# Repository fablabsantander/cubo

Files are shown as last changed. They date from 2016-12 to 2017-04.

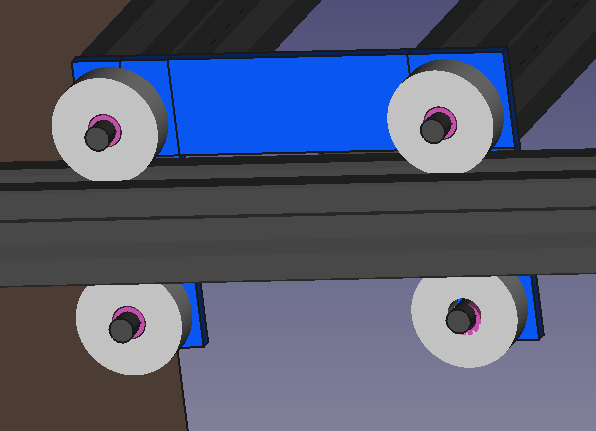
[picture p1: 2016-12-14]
IMG/image-1.png

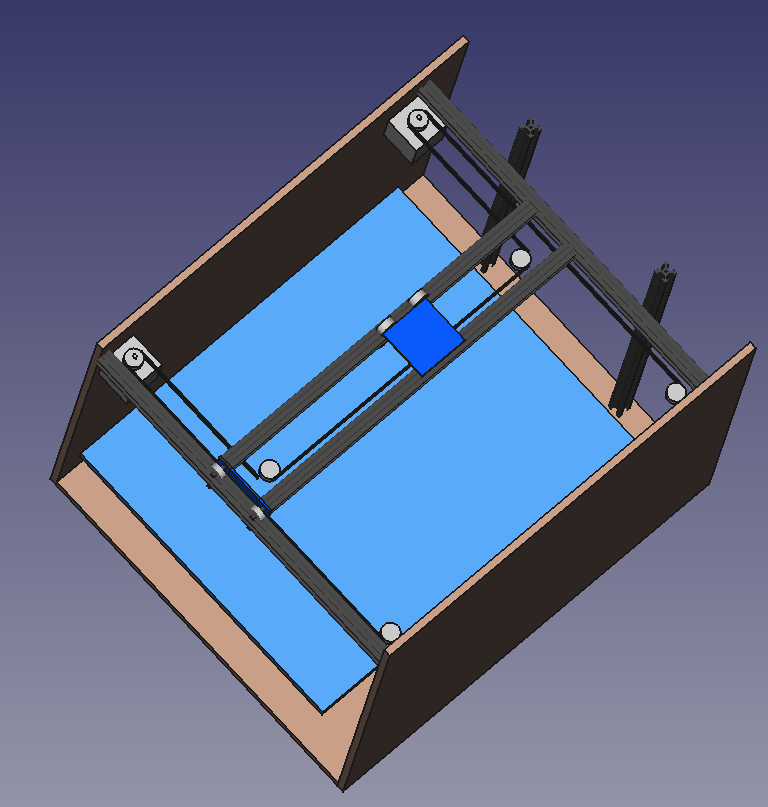
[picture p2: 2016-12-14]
IMG/image.png

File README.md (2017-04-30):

# cubo
cubo design
real build

Machine for 3D printing (and laser engraving).

Some members of the FabLab Santander have committed themselves to build the machines of the lab in a co-creation process.
This machine is a cubic shape 3D printer with option of laser engraving.
This side size of the cube is more or less 500mm.
The purpose of the design is to get a big size open source 3D printer, nice-looking, easy to build, robust with metal profiles and standart bearings (not the linear ones...).
The main design software is openscad which allow a natural integration in CVS or github software repositories.
The design is parametrized as much as possible. The elements choosen for the first version are:

- RatRig profiles
- 627 bearings
- wood/plexiglass plates
- complex pieces are 3D printed
- the XY movement follow the "coreXY" scheme (see www.corexy.com)

Coding conventions for openscad files:
- try to comment every decision in the design
- try to use parameters for all dimensions such we have not to redesign when changing one piece dimension.
- minimize the number of parameters
- put the parameters at the beginning of the file with explicit names and comments
- then put the modules to be 3D printed (commented)
- then put the module called "ensemble" that gather all the pieces
- then put eventually cut views
- then put the modules

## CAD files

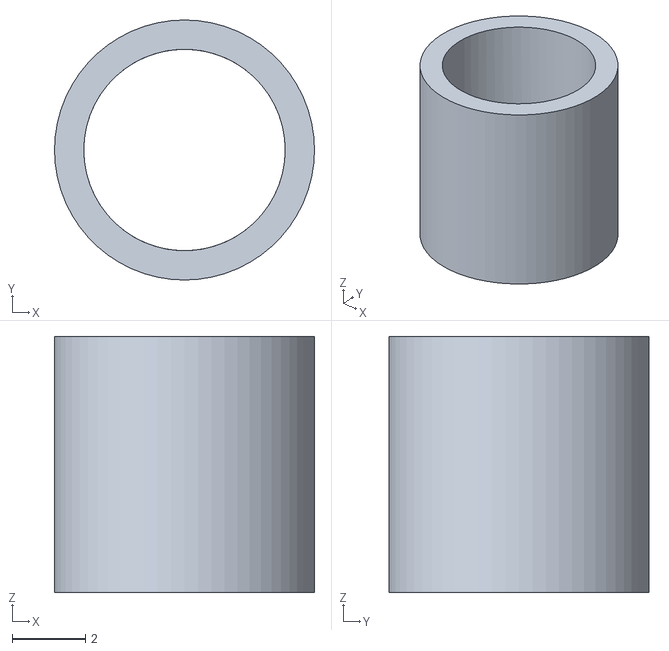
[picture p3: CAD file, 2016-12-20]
anillo_rodamiento_627.obj
7.10 x 7.10 x 7.00

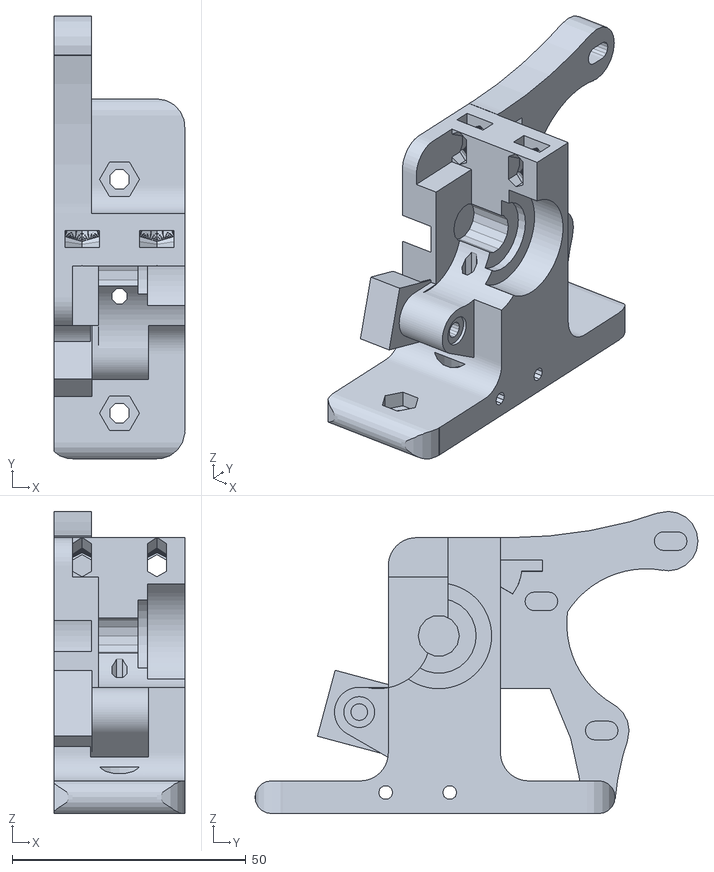
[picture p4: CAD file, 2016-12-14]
extruder.stl
28.0 x 94.7 x 64.6

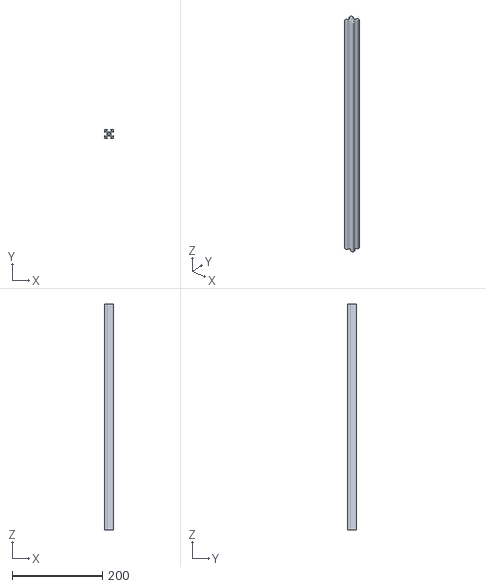
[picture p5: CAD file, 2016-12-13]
profil_ratrig_500mm.stl
20.0 x 20.0 x 500.0

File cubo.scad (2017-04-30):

//FabLab Santander
//machine "cubo"
//licence creative common 

//profile:
profilex_length=500;
profiley_length=500;
profilez_length=500;
profile_size=20;
profile_screw_D=5;

// height
h=560;//side plate height

//plates :
th=10; //side and base plate thickness
back_th=3;//back plate thickness


//bearing 627:
bearing_D=22;
bearing_dint=7;
bearing_th=7;



//distance between the 2 guides x
inter_guides_x=profiley_length/2+10+bearing_th/2;
echo("distance between the 2 guides x:",2*inter_guides_x,"mm");
//x trail:
dx_guidey=60;//distance between the 2 guides y
dz_guidey=profile_size/2+bearing_D/2-1.5;//profile_size-0.5;
//x trail plate:
xtrailPlateThickness=3;
//head:
headPlateThickness=5;
headPlate_dx=dx_guidey-profile_size-2;
headPlate_dy=80;

//stepper motor nema17:
motNema17Side=42;
motNema17Dep=47.65;
motNema17AxisD=5;
motNema17AxisL=26;
motNema17ScrewFixD=3;
motNema17ScrewsDist=31;
motNema17FrontD=22;
motNema17FrontH=1.5;
//motor pulley GT2
pulleyTeethDiameter=12;
pulleyDiameter=16;
pulleyThickness=16;
//belts:
belt_th=6;//belt thickness
belt_thi=2;//belt thickness
z_belts=3;
//half distance between pulley in y direction
inter_pulleys_y=profiley_length*0.46;
//head plateform parameters:
head_bearing_axis_z=profile_size/2+bearing_D/2-1.5;

//PLA coil:
d_PLA_coil_inner=51;
d_PLA_coil_outer=200;
h_PLA_coil=72;


head_X=150;
head_Y=0;



//the CUBE machine mounted:
//ensemble();
//structure();


//------------  3D print: -------------------
//rotate([-90,0,0])xtrailPlate();
//bearingPusher();
//bearingAdaptor(); 
//stepper_holder();
//pulley_holder();
//rotate([180,0,0])head_plateform();
//rotate([-90,0,0])head_bearing_holder();
//pulley_washer();
//rotate([90,0,0])PLA_pulley_holder();
//rotate([0,90,0])PLA_pulley();
PLA_coil_holder();
//------------  3D print: -------------------

//dim cube:
cube_length_x = profilex_length+2*thickness_panel;
cube_length_y = profiley_length+2*profile_size;
h_stop_extruder = 120;
height_cube = profilex_length+h_stop_extruder+2*thickness_panel;

//z system:
inter_zguides=300;




module plates()
{
//translate([profilex_length/2,0,0]) provisory_side_plate();
//mirror([1,0,0])translate([profilex_length/2,0,0]) provisory_side_plate();
//translate([profilex_length/2,0,0]) side_plate();
//for (c=[0,1]) mirror([c,0,0])translate([profilex_length/2,0,0]) side_plate();

//side metalic bar for the XY system		
bar_th=4; 

//front plate:
dx=profilex_length+2*bar_th;
l3=130;//front plate height

dx_base=profilex_length+2*th+2*bar_th;
dy=profiley_length+50;
//l1=100; //side plates width
h2=200;//side plate noze height
backSpace=50;//space at the back for the Z system
dy2=profiley_length+50;//side plate depth
dy_nose=dy2*0.25;//nose depth
rad=dy_nose/2;
hup=profile_size*2.5;
	
//side metalic bar for the XY system 
color([0.8,0.8,0.8])for (c=[0,1]) mirror([c,0,0])
{
	difference()
	{
	translate([profilex_length/2,-dy2/2,-profile_size/2])cube([bar_th,dy2,profile_size]);
	for (y=[-1,1])translate ([profilex_length*0.3,y*(inter_guides_x),0])rotate([0,90,0])cylinder(h=200,r=5/2,$fn=20);	}
}
color=[.6,.6,.9];
//base plate:
color(color+[0.1,0,0]) translate([-dx_base/2,-dy2/2+dy_nose,-h])cube([dx_base,dy2-dy_nose+backSpace,th]);
//front plate;
//color(color-[0.1,0,0])translate ([-dx/2,-dy2/2+dy_nose,-h+th])rotate([16,0,0]) cube([dx,th,l3]);

//back plate;
color(color-[0.1,0,0])translate ([-dx/2-th,-dy2/2+dy_nose+dy2-dy_nose+backSpace,-h])cube([dx+2*th,back_th,hup+h]);

//side plates
color(color)for (c=[0,1]) mirror([c,0,0])translate([profilex_length/2+th+bar_th,0,0]) 
{
rotate([0,-90,0])linear_extrude(height=th)
	{
	polygon([
		// z  y
		[-profile_size*4,-dy2/2],
		[hup,-dy2/2],
		[hup,dy2/2+backSpace],
		[-h+th,dy2/2+backSpace],
		[-h+th,-dy2/2+dy_nose]
		]);
	}
}
//side plates
//for (c=[0,1]) mirror([c,0,0])translate([profilex_length/2,0,0]) 
//	{
//	color("orange")
//	difference()
//		{
//		union()
//			{
//			//top:
//			translate ([0,-dy2/2,-h2+20]) cube([thickness_panel,dy2,h2]);
//			//bottom:	
//			translate ([0,-dy2/2+dy_nose,-h+20]) cube([thickness_panel,dy2-dy_nose,h]);
//			//round
//			translate ([0,-dy2/2+rad,-h*0+20-h2])rotate([0,90,0])cylinder(r=rad,h=th,$fn=30);
//			}
//		for (y=[-1,1])translate ([profilex_length*0.3,y*(inter_guides_x),0])rotate([0,90,0])cylinder(h=200,r=5/2,$fn=20);
//		}
//	}



echo("base plate size (mm):",dx_base,dy2-dy_nose+backSpace,th);
echo("side plates (2x) size (mm):",dy2/2+backSpace-(-dy2/2),hup-(-h+th),th);
echo("dy nose (mm):",dy_nose);
//echo("back plate size (mm):",dx-2*th,l2,th);
echo("front plate size (mm):",dx,l3,th);

	
}




module ensemble()
{
//the clothes of the machine:
//cover();
    
plates();

provisory_zsystem();
 
	
//guides for x translation
for (i=[-1,1])
translate([-profilex_length/2,i*(-profiley_length/2-10-bearing_th/2),0])rotate([0,90,0])color([0.2,0.2,0.2])import ("profil_ratrig_500mm.stl");

//guides for y translation
translate([head_X,0,0])//Y carriage ensemble
{
for (i=[-1,1])
    {
    //guides y
    translate([i*-dx_guidey/2,profiley_length/2,dz_guidey])rotate([90,0,0])color([0.2,0.2,0.2])import ("profil_ratrig_500mm.stl");
    //bearings:
    for (j=[-1,1]) translate([i*-dx_guidey/2,j*(profiley_length/2+bearing_th/2+10),dz_guidey])rotate([90,0,0])
        {
        bearing();
        bearingAdaptor();    
        }
    //screw for bearings:
     color([0.4,0.4,0.4])for (j=[-1,1])translate([i*-dx_guidey/2,j*(profiley_length/2+10),dz_guidey])rotate([90,0,0])cylinder(r=profile_screw_D/2,h=20,$fn=30,center=true);
    }
	 
//lower bearings 
for (j=[-1,1]) translate([0,j*(profiley_length/2+bearing_th/2+10),-dz_guidey])
	{
	rotate([90,0,0])bearing();
	rotate([90,0,0])bearingAdaptor();    
	//screw for bearings:
	color([0.4,0.4,0.4])translate([0,-profile_size/2,0])rotate([90,0,0])cylinder(r=profile_screw_D/2,h=30,$fn=30,center=true);
   }
	 
	 
	 
//xtrail side plates:
translate([0,profiley_length/2+xtrailPlateThickness/2,dz_guidey+profile_size/2])
	{
	xtrailPlate();
	bearingPusher();
	}
mirror([0,1,0]) translate([0,profiley_length/2+xtrailPlateThickness/2,dz_guidey+profile_size/2])
	{
	xtrailPlate();
	bearingPusher();
	}
  
//head:
translate([0,head_Y,dz_guidey])
	{
	//bearings
	 for (x=[-1,1]) for (y=[-1,1]) translate([x*dx_guidey/2,y*headPlate_dy*0.4,head_bearing_axis_z])rotate([0,0,90]) rotate([90,0,0])bearing();
	 for (x=[-1,1])  translate([x*dx_guidey/2,0,-head_bearing_axis_z])rotate([0,0,90]) rotate([90,0,0])bearing();
	//head plateform:
	head_plateform();
	//head bearings holder (with springs to push down the bearings
	for (y=[-1,1])translate([0,y*headPlate_dy*0.44,head_bearing_axis_z])head_bearing_holder();
	 // extuder:    
	//prusa i2 extruder:
	//translate([0,0,headPlateThickness])color("blue")rotate([0,0,0])import("extruder.stl");  
	//extruder head alone:
	color("gray")translate([0,0,5])extruder();  
	}

//pulleys fixed on the Y guides:
for (x=[-1,1])for (y=[-1,1])translate([-x*dx_guidey/2,y*(profiley_length*0.45-bearing_D),z_belts]) 
		{
		bearing();
		translate([0,0,-bearing_th])pulley_washer();
		}
}//end of X carriage ensemble

translate([0,0,z_belts])
{

for (c=[0,1]) mirror([0,c,0])
	{
	//stepper holder:
	translate([-profilex_length/2+motNema17Side/2,inter_pulleys_y,-17])stepper_holder();
	//pulley holder:
	translate([profilex_length*0.47,-inter_guides_x-profile_size/2,-17])pulley_holder();
	}

for (y=[-1,1])
	{
	//stepper motors:
	translate([-profilex_length/2+motNema17Side/2,y*inter_pulleys_y,-17])rotate([0,-90,0])color("skyblue")motor_nema17();
	//GT2 pulleys on steppers:
	color("grey")translate([-profilex_length/2+motNema17Side/2,y*inter_pulleys_y,-pulleyThickness*0.7]) pulley();//bearing();
	//pulleys on the other side:
	translate([profilex_length*0.47,y*inter_pulleys_y,0]) bearing();
	}
	
	//pulleys on the other side:
	for (c=[0,1]) mirror([0,c,0])translate([profilex_length*0.42,inter_pulleys_y-20,0]) bearing();
	
	


//belt at right
color("blue")for (c=[0,1]) mirror([0,c,0])translate([profilex_length*0.47+bearing_D/2,inter_pulleys_y*0.05,-belt_th/2])rotate([2,0,0])cube([belt_thi,inter_pulleys_y*1.9,belt_th],center=true);
//belts:
for (y=[-1,1])
	{
	color("blue")translate([-profilex_length/2+motNema17Side/2,y*(inter_pulleys_y+bearing_D/2),-belt_th/2])cube([inter_pulleys_y*2,belt_thi,belt_th]);
	color("blue")translate([-profilex_length/2+motNema17Side/2,y*(inter_pulleys_y-bearing_D/2),-belt_th/2])cube([profiley_length/2,belt_thi,belt_th]);
	color("blue")translate([head_X+dx_guidey/2,y*(inter_pulleys_y-bearing_D/2),-belt_th/2])cube([profiley_length/2-head_X-dx_guidey,belt_thi,belt_th]);
	}
//belts on the x rail:
color("blue")for (x=[-1,1]) translate([head_X-x*dx_guidey/2+x*bearing_D/2,-inter_pulleys_y+bearing_D,-belt_th/2])cube([belt_thi,inter_pulleys_y*2-bearing_D*2,belt_th]);

}

translate([-profilex_length/2+40,-100,-h+th])rotate([0,0,90])
{
PLA_pulley_holder();
PLA_pulley();
}

translate([0,0,-h+th])rotate([0,0,90])
{
color("black")translate([0,0,5])PLA_coil();
PLA_coil_holder();
}



}
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

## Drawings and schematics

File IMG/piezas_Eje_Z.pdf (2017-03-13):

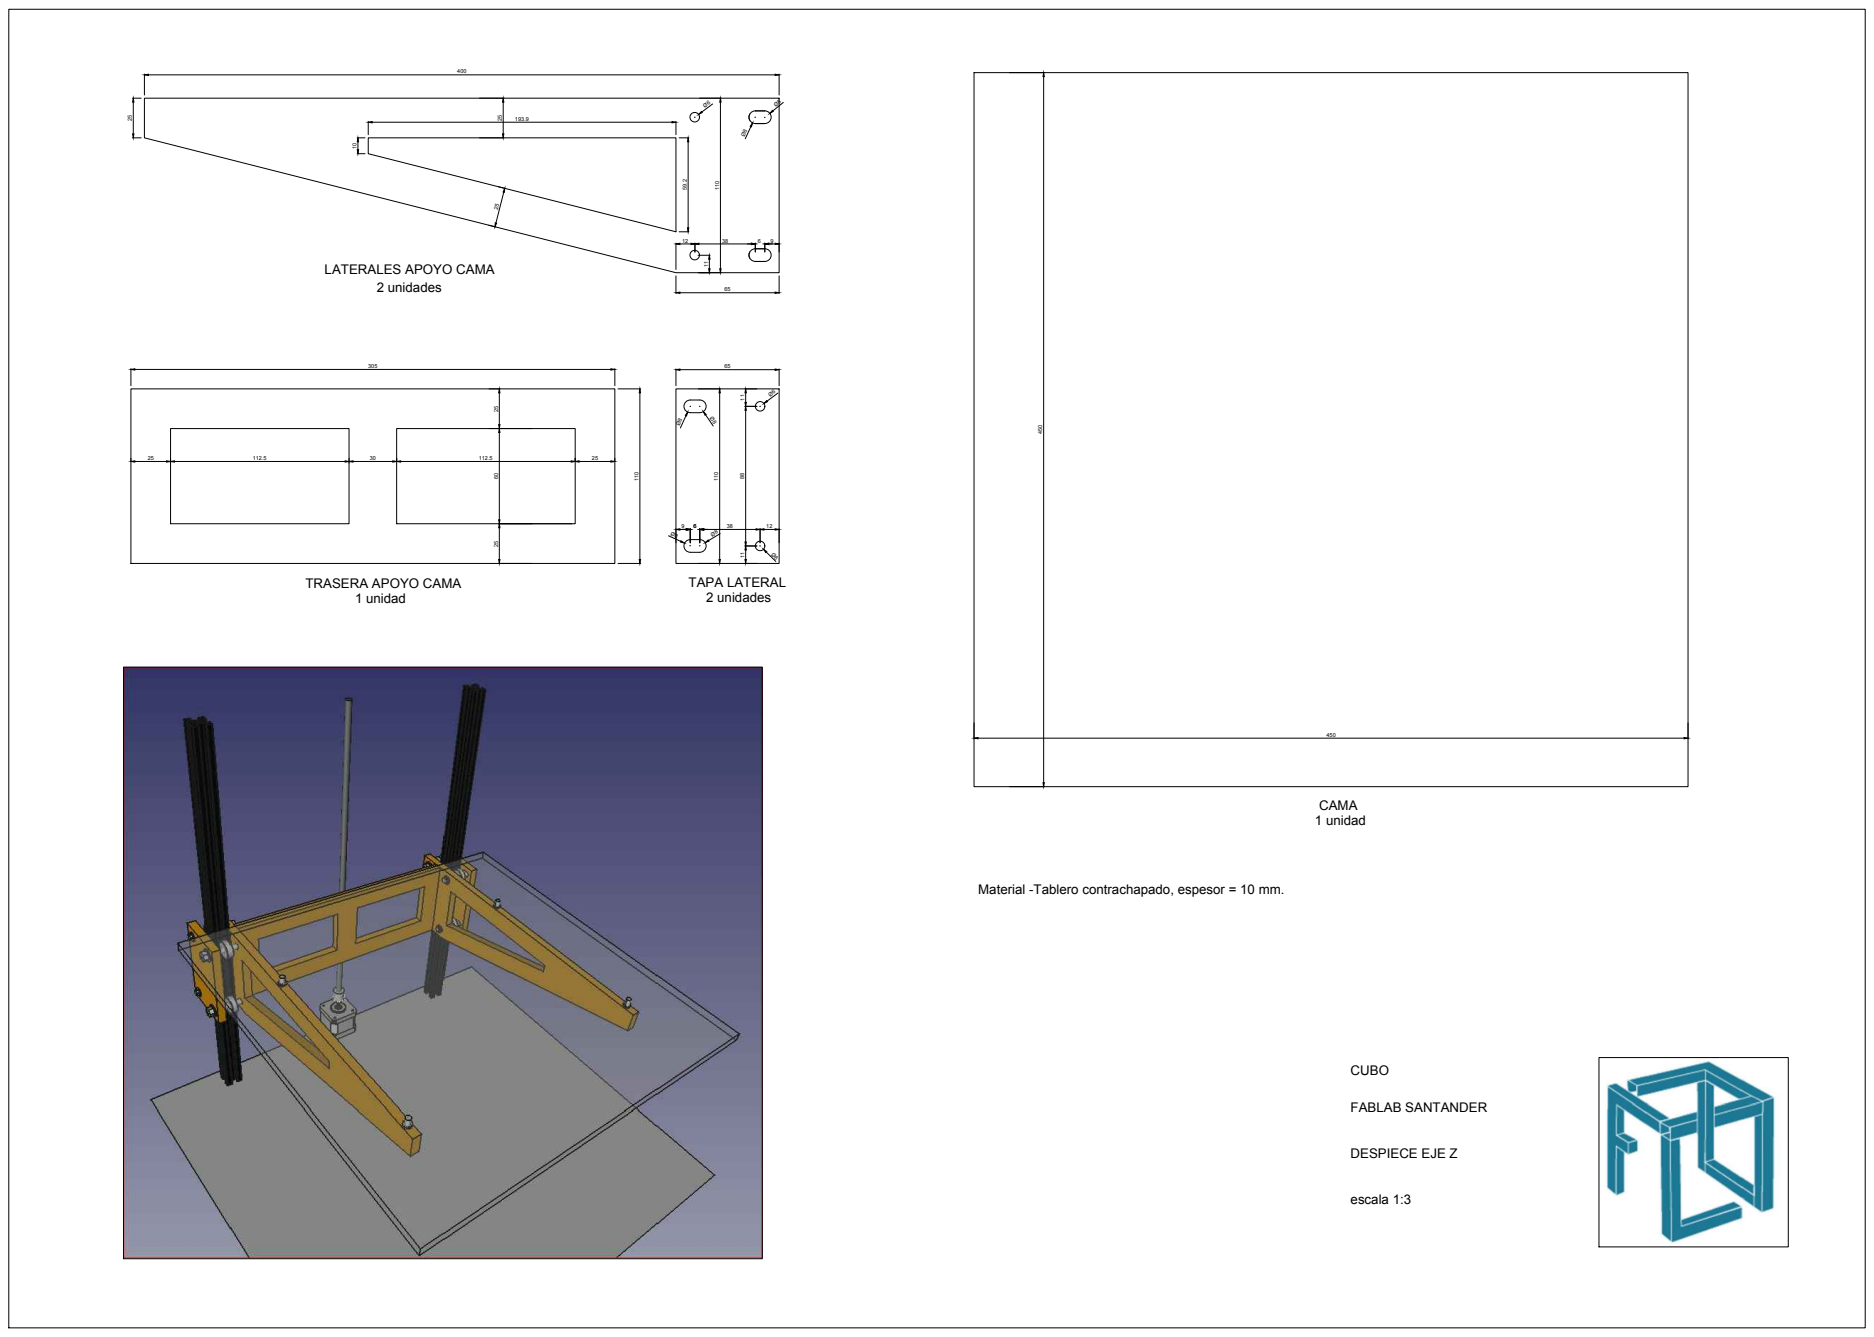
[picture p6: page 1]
DESPIECE EJE Z; escala 1:3; FABLAB SANTANDER; TAPA LATERAL; 2 unidades; 1 unidad

LATERALES APOYO CAMA

TRASERA APOYO CAMA

Material -Tablero contrachapado, espesor = 10 mm.

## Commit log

2016-12-13 primera versión
    primera versión fichero cubo.scad y un perfil ratrig todo hecho de 500mm
    [cubo.scad, profil_ratrig_500mm.stl]
2016-12-13 he puesto los rodamientos movimiento x
    [cubo.scad]
2016-12-14 He añadido una carpeta para incluir imagenes.
2016-12-14 placas de lado del carro X
    [cubo.scad]
2016-12-14 he puesto un extrusor de prueba
    [cubo.scad, extruder.stl]
2016-12-14 corregido un error en las placas
    [cubo.scad]
2016-12-19 Diseño primer prototipo del cubo contenedor de madera
    Las dimensiones del cubo dependen totalmente de la longitud de los
    perfiles RatTrig y del espesor de los paneles de madera.
    [cubo.scad]
2016-12-20 nuevo sistema de aprieto del rodamiento
    [cubo.scad]
2016-12-20 he repuesto las tablas de madera ! (oops)
    [cubo.scad]
2016-12-20 reglas para el fichero scad en readme
2016-12-20 reglas de codificacion openscad
2016-12-20 reglas de codificacion
2016-12-20 He reorganizado el codigo, ver modulo "cover()"
    [cubo.scad]
2016-12-20 anillo para adaptar el rodamiento 627
    anillo para adaptar el rodamiento 627 a un tornillo M5
    [anillo_rodamiento_627.obj]
2016-12-20 Ajuste de la distancia en Z de los rodamientos
    Una prueba de impresión me ha permitido medir de manera mas exacta la buena distancia en Z de los rodamientos.
    [cubo.scad]
2017-01-20 sistema motores
    he puesto los motores X+Y, las poleas y las correas
    [cubo.scad]
2017-01-27 tablas para probar el sistema X+Y
    [cubo.scad]
2017-02-02 soportes de los motores X+Y
    [cubo.scad]
2017-02-02 soportes de poleas
    he puesto los soportes de poleas del otro lado de los motores
    [cubo.scad]
2017-02-05 diseno de la cabeza y poleas
    diseno de la cabeza y sistema de poleas mas completo siguiendo el esquema "coreXY"
    [cubo.scad]
2017-02-05 enlace con la pagina corexy.com
2017-03-10 soporte para el extrusor
    [cubo.scad]
2017-03-10 pequeña corrección
    [cubo.scad]
2017-03-13 Planos de despiece del eje Z
    Planos en formatos SVG y PDF
2017-03-24 estructura de prueba
    [cubo.scad]
2017-04-06 he puesto las tablas finales
    [cubo.scad]
2017-04-10 placas mas bonitas, cama y barras de fijacion
    barras para fijar los railes X , asi se puede desmontar la parte superoir de la impresora sin rollo !
    [cubo.scad]
2017-04-30 PLA coil holder and PLA pulley
    [cubo.scad]
